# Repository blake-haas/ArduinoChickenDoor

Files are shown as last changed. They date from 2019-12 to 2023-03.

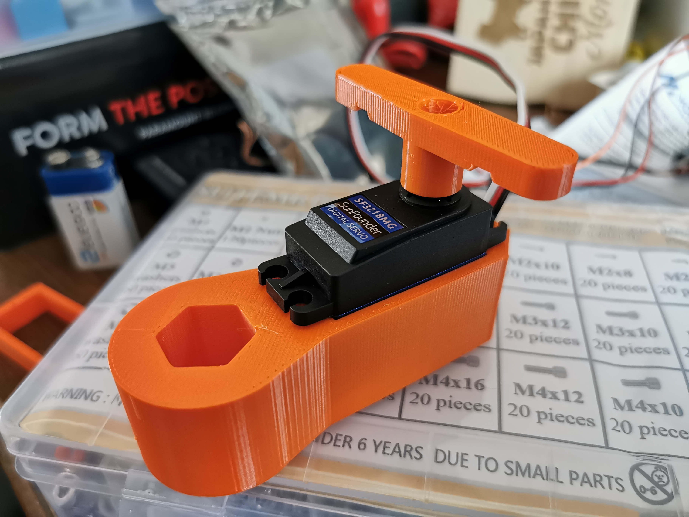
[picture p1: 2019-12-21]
IMG_20191218_131732.jpg

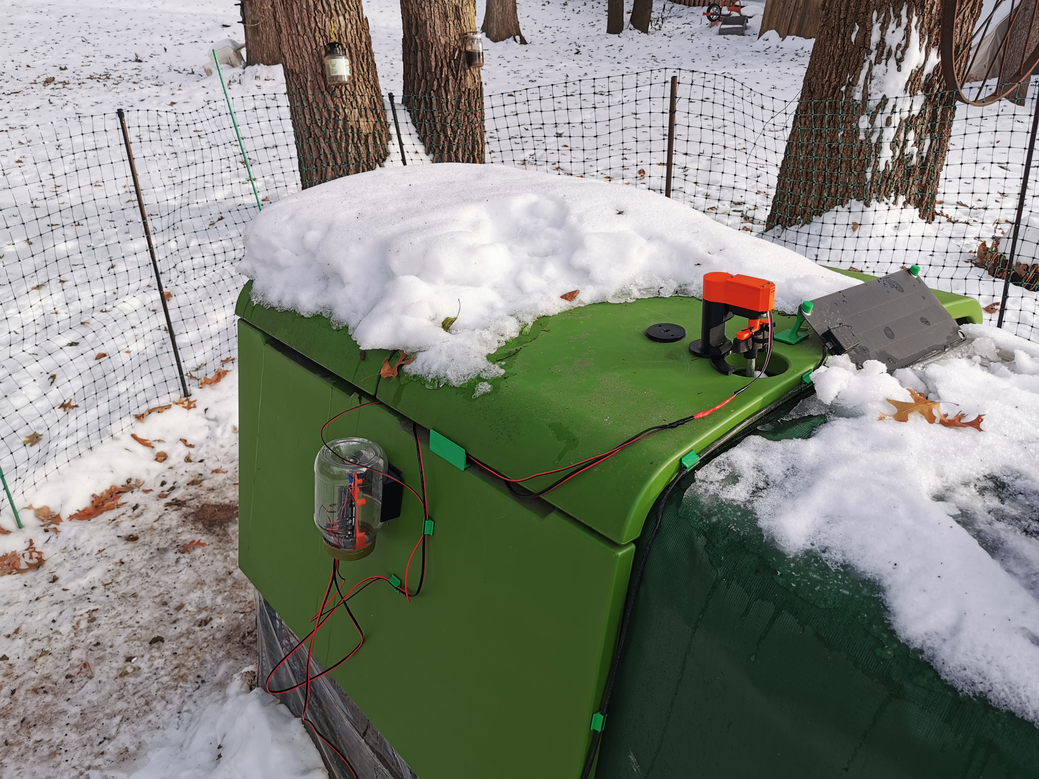
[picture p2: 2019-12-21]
IMG_20191221_142228.jpg

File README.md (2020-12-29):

# ArduinoChickenDoor
Automatic door for chicken coop (eglu cube) | Can be adapted to work with any coop.
Designed for very low power usage.

This is a project for an automatic chicken door based on light levels.
Door closes at around 19 lux and opens after 50 lux.

Parts list:
1. Arduino Uno / Mini / micro
2. SunFounder 20KG Servo Motor Waterproof High Torque Servo, SF3218MG Metal Gear Digital Servo
3. LM393 Digital Light Intensity Photosensitive Sensor Module for Arduino UNO
4. Power source 9v / 12v. For me it was a 12v tractor battery with a LM2596s Buck Converter tuned to 9v. 
5. Wires and a clear container to mount the light sensing hardware (mayo jar for me).
6. A 3d printer to print my designed parts for the eglu cube or your own diy solution for your coop.
7. Misc M2, M3 and M4 bolts for my designed parts.
8. Silicone / Gasket maker to seal the servo body if using my designed parts (Not Necessary if using ServoCoverBody_ClosedTop).

This has lasted through a winter and is doing great!
Enancements after summer and winter use:
I RECOMMEND USING THE ServoStand_v2_Short.stl WITH THE ServoHandleAdapter.stl. It has better alignment and smoother operation!
CHECK OUT THE WIRE DIAGRAM (AutoChickenDoorCoopWireDiagram.png) for the simplest installation.

Get a metal T spline Metal Aluminum 25T Servo Horn, the printed one will eventually fail.

Wire in a 5vdc converter to have a solid 5v off of the main 9v power vs having the arduino try to handle the load (my uno handles it but just barely).

I also wired up some 3 Pin Way Car Waterproof Wire Connector Plug Auto Electrical Wire Connectors so that i can easily disconnect the system if i needed
to troubleshoot anything.

I added some DIY Battery Pack PVC Heat Shrink Wrap Tube 180±3MM to the jar on the bottom third to act like a skirt to allow water to flow AWAY
from the jar lid. This keeps the entire inside of the jar bone dry while still allowing me to unscrew the lid for access.

Im located in minnesota. I upgraded my power source (battery) to a full 12v car battery to power this thing and i use a 30w solar panel to trickle charge it all day.
It works flawlessly this way all summer. In the winter i have a trickle charger plugged in via extension cord to keep it topped off.

Lastly, I covered the uno and electronics in some clear nail polish to protect from moisture (just in case).

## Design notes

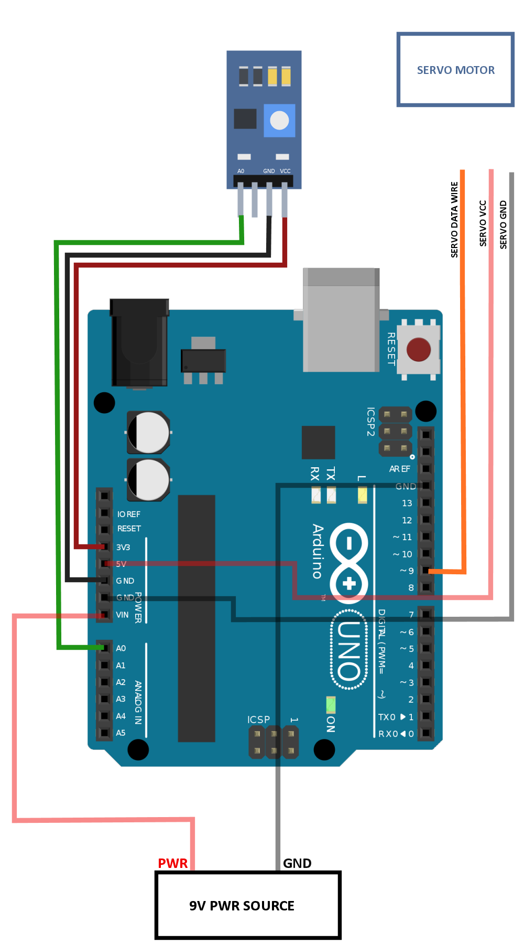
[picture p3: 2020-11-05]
AutoChickenDoorCoopWireDiagram.png

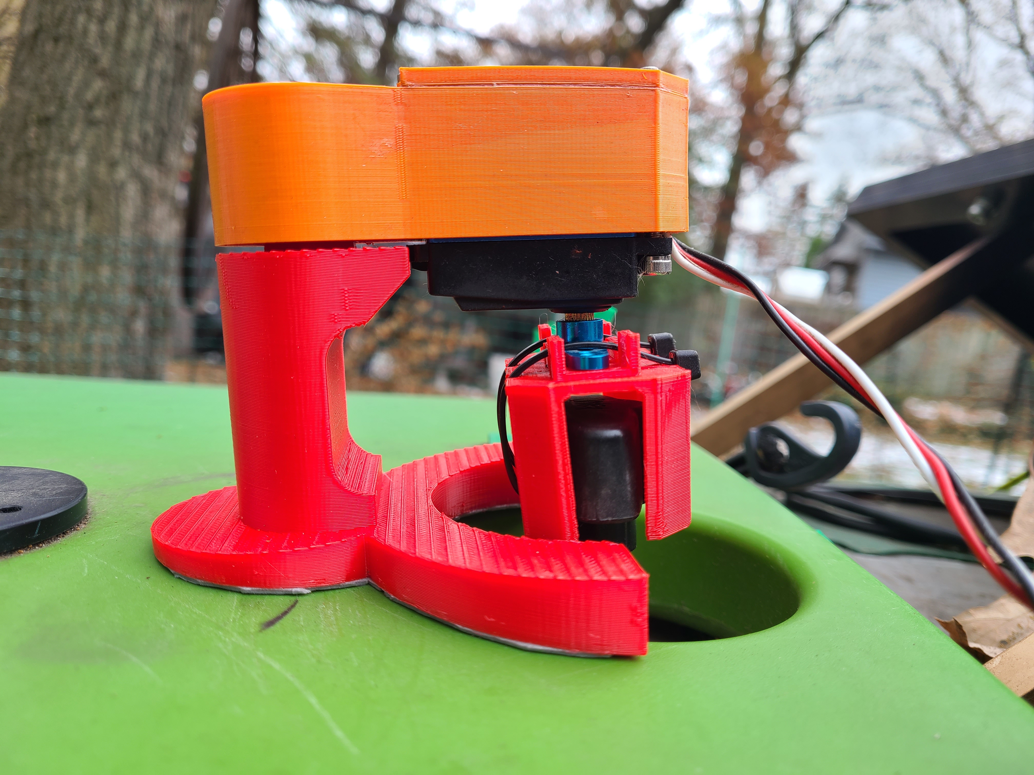
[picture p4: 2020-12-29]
2020-10-29 10.03.07.jpg

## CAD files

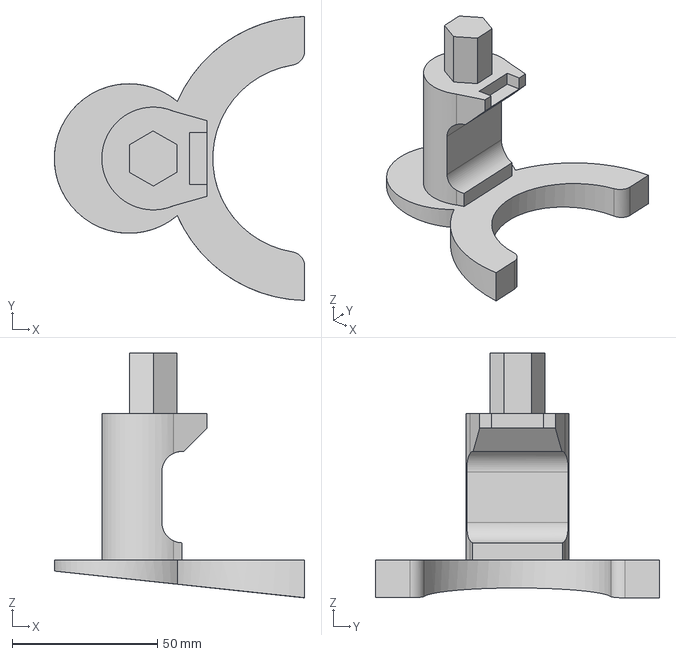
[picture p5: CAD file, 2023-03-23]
ChickenCoopServoBaseV2.step
86.1 x 97.6 x 84.2 mm

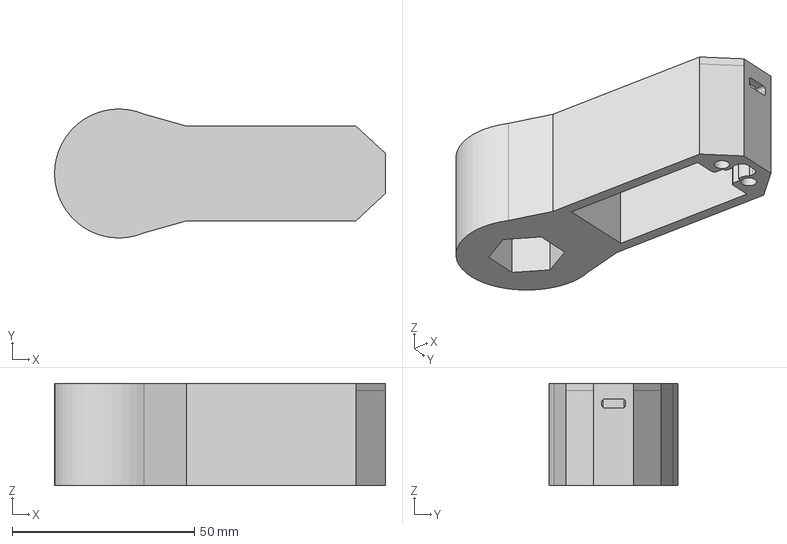
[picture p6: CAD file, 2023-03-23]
ChickenCoopServoCoverBodyModel.step
90.8 x 35.3 x 28.0 mm

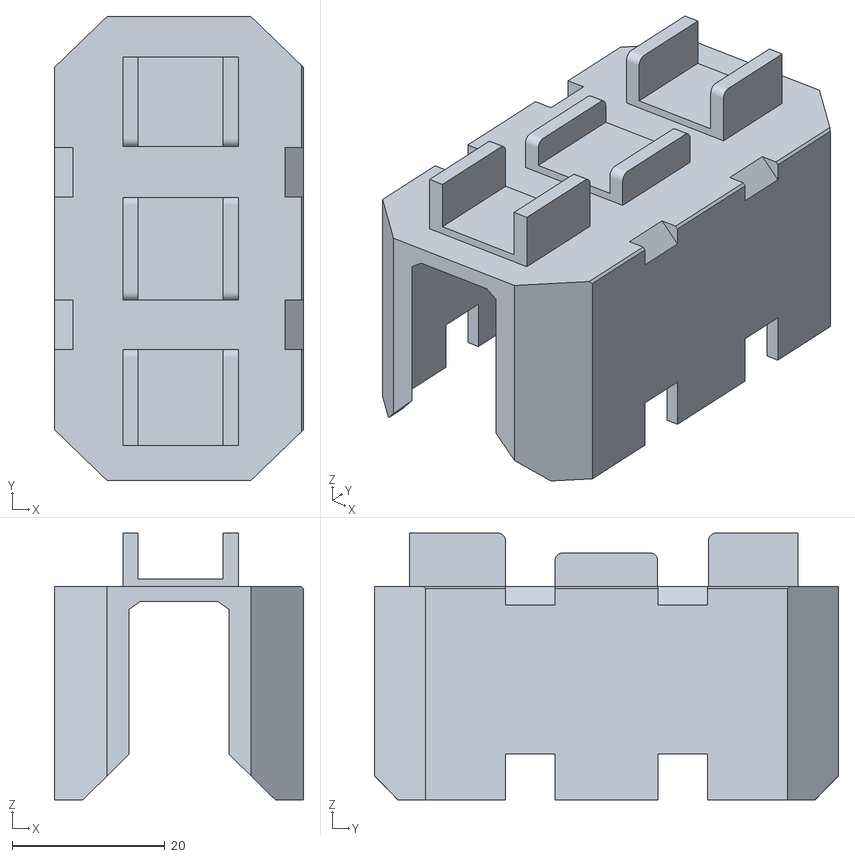
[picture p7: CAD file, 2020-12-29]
ServoHandleAdapter.stl
32.7 x 60.8 x 35.0

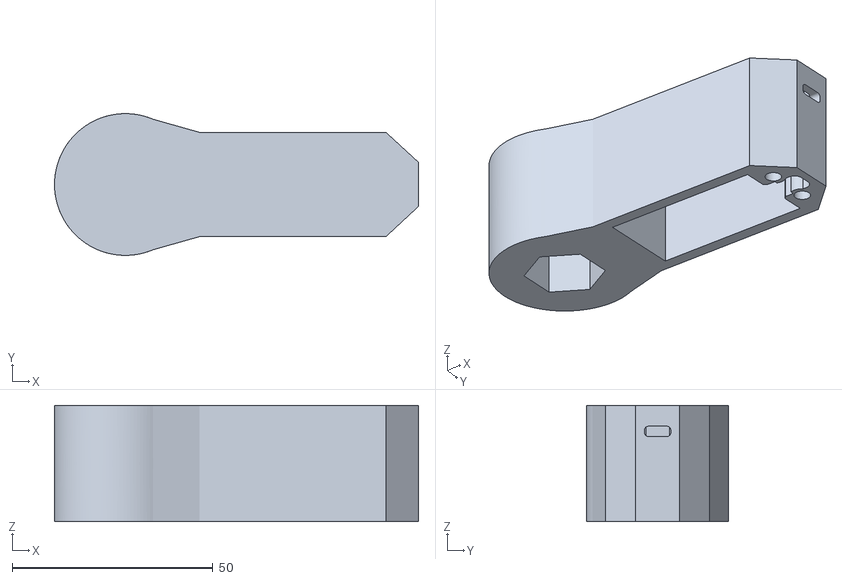
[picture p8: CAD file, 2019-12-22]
ServoCoverBody_ClosedTop.stl
90.8 x 35.3 x 29.0

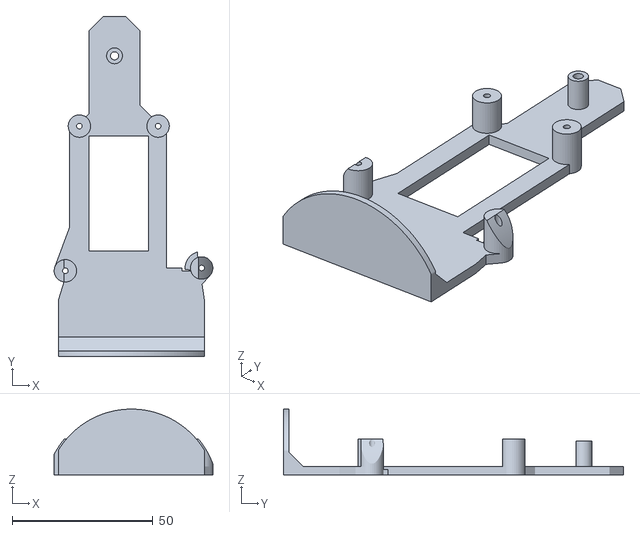
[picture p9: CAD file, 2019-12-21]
ArduinoUnoMountMayoJarLid.stl
56.5 x 121.0 x 23.4

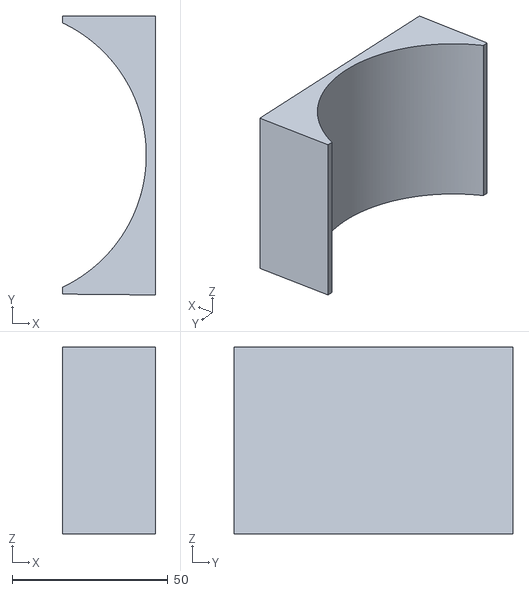
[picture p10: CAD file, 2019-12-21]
JarAttachment.stl
30.0 x 89.7 x 60.0

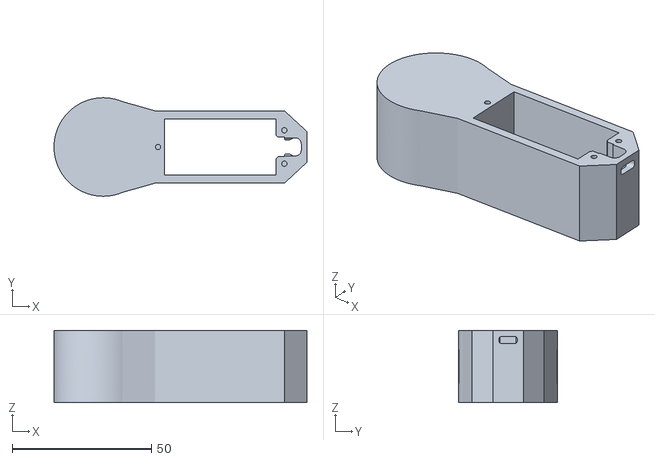
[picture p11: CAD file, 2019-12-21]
ServoCoverBody.stl
90.8 x 35.4 x 26.0

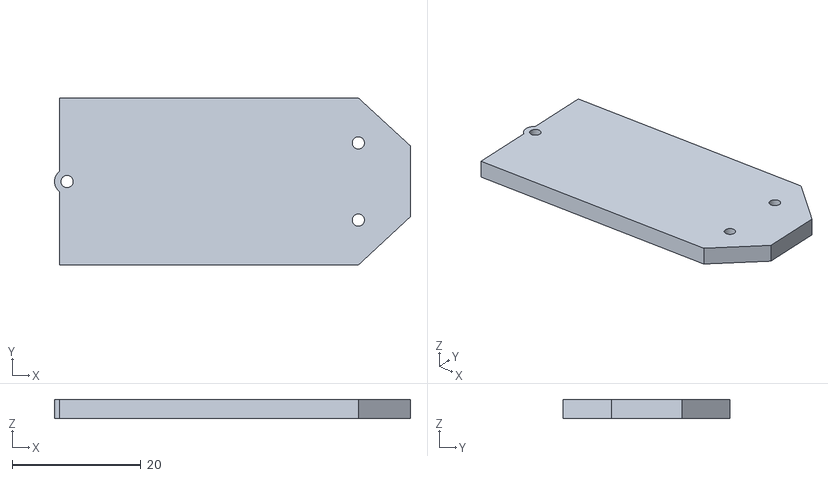
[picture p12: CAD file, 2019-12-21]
ServoCoverTop.stl
55.4 x 26.0 x 3.00

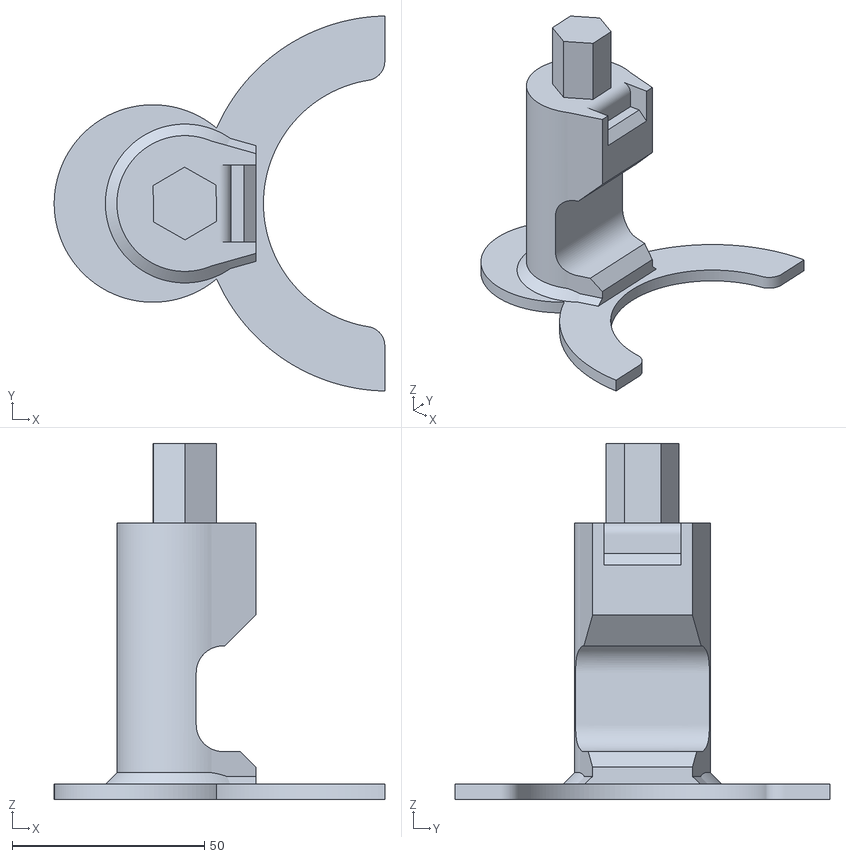
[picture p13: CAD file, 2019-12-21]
ServoStand.stl
86.1 x 97.6 x 92.7

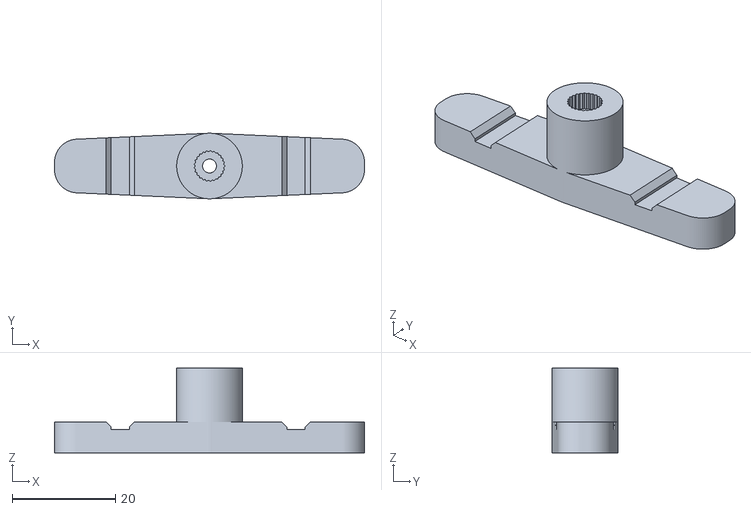
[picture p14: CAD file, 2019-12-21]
ServoHub.stl
60.0 x 12.7 x 16.4

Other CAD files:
ServoStand_v2_Short.stl

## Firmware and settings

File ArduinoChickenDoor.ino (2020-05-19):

#include <Servo.h>
#include <avr/wdt.h>            // library for default watchdog functions
#include <avr/interrupt.h>      // library for interrupts handling
#include <avr/sleep.h>          // library for sleep
#include <avr/power.h>          // library for power control

int SERVO_PIN = 9;
int LIGHT_SENSOR_ANALOG_PIN = A0;
int LOW_LIGHT_THRESHOLD = 500; // ~1.3 lux You need to calibrate this against a lux meter, each sensor has its own resistance values.
int HIGH_LIGHT_THRESHOLD = 210; // ~24 lux
int HIGH_LIGHT_HIT_COUNT = 15; // 15 min
int LOW_LIGHT_HIT_COUNT = 20; // 20 min
int LowLightCount = 0;
int HighLightCount = 0;
int DoorState = 0; // 0 is unknown // 1 is open // 2 is closed
int pos = 25;
Servo Servo1;
int nbr_remaining; // how many times remain to sleep before wake up 

// interrupt raised by the watchdog firing
// when the watchdog fires during sleep, this function will be executed
// remember that interrupts are disabled in ISR functions
ISR(WDT_vect)
{
        // not hanging, just waiting
        // reset the watchdog
        wdt_reset();
}
// function to configure the watchdog: let it sleep 8 seconds before firing
// when firing, configure it for resuming program execution
void configure_wdt(void)
{
 
  cli();                           // disable interrupts for changing the registers

  MCUSR = 0;                       // reset status register flags

                                   // Put timer in interrupt-only mode:                                       
  WDTCSR |= 0b00011000;            // Set WDCE (5th from left) and WDE (4th from left) to enter config mode,
                                   // using bitwise OR assignment (leaves other bits unchanged).
  WDTCSR =  0b01000000 | 0b100001; // set WDIE: interrupt enabled
                                   // clr WDE: reset disabled
                                   // and set delay interval (right side of bar) to 8 seconds

  sei();                           // re-enable interrupts

  // reminder of the definitions for the time before firing
  // delay interval patterns:
  //  16 ms:     0b000000
  //  500 ms:    0b000101
  //  1 second:  0b000110
  //  2 seconds: 0b000111
  //  4 seconds: 0b100000
  //  8 seconds: 0b100001
 
}
// Put the Arduino to deep sleep. Only an interrupt can wake it up.
void sleep(int ncycles)
{  
  nbr_remaining = ncycles; // defines how many cycles should sleep

  // Set sleep to full power down.  Only external interrupts or
  // the watchdog timer can wake the CPU!
  set_sleep_mode(SLEEP_MODE_PWR_DOWN);
 
  // Turn off the ADC while asleep.
  power_adc_disable();
 
  while (nbr_remaining > 0){ // while some cycles left, sleep!

  // Enable sleep and enter sleep mode.
  sleep_mode();

  // CPU is now asleep and program execution completely halts!
  // Once awake, execution will resume at this point if the
  // watchdog is configured for resume rather than restart
 
  // When awake, disable sleep mode
  sleep_disable();
  
  // we have slept one time more
  nbr_remaining = nbr_remaining - 1;
 
  }
 
  // put everything on again
  power_all_enable();
 
}
void setup() {
  // put your setup code here, to run once:
  //Serial.begin(115200);
  //while (! Serial) {}  // wait for serial monitor to attach
  // Initialize the door open.
  openDoor();
  delay(20);
  // configure the watchdog
  configure_wdt();
}

void loop() {
  int16_t currentLightLevel = analogRead(LIGHT_SENSOR_ANALOG_PIN);
  setLightLevel(currentLightLevel);
  if (HighLightCount == HIGH_LIGHT_HIT_COUNT && DoorState != 1) {
//    Serial.print("HighLightCount: ");
//    Serial.print(HighLightCount);
//    Serial.println("");
//    Serial.print("LowLightCount: ");
//    Serial.print(LowLightCount);
//    Serial.println("");
//    Serial.println("opening door!");
//    Serial.print("Previous DoorState: ");
//    Serial.print(DoorState);
//    Serial.println("");
    // Open the Door
    openDoor();
  }
  if (LowLightCount == LOW_LIGHT_HIT_COUNT && DoorState != 2) {
//    Serial.print("HighLightCount: ");
//    Serial.print(HighLightCount);
//    Serial.println("");
//    Serial.print("LowLightCount: ");
//    Serial.print(LowLightCount);
//    Serial.println("");
//    Serial.println("closing door!");
//    Serial.print("Previous DoorState: ");
//    Serial.print(DoorState);
//    Serial.println("");
    // Close the Door
    closeDoor();
  }
  sleep(8); // sleep for 1 min..
}
void setLightLevel(int16_t level) {
  if (level >= LOW_LIGHT_THRESHOLD) {
    // We got a low light value, RESET the high count
    HighLightCount = 0;
    LowLightCount = LowLightCount + 1;
    if (LowLightCount < LOW_LIGHT_HIT_COUNT) {
      // stop incrementing
      LowLightCount = LowLightCount + 1;
    }
  } else if (level <= HIGH_LIGHT_THRESHOLD) {
    // We got a high light value, RESET the low count
    LowLightCount = 0;
    if (HighLightCount < HIGH_LIGHT_HIT_COUNT) {
      // stop incrementing
      HighLightCount = HighLightCount + 1;
    }
  }
//  Serial.print("Lux: ");
//  Serial.print(level);
//  Serial.println("");
}
void openDoor() {
  Servo1.attach(SERVO_PIN, 500, 2500);
  for (pos = 160; pos >= 25; pos -= 1) {
    // goes from 160 degrees to 25 degrees
    // in steps of 1 degree
    Servo1.write(pos);
    delay(50);
  }
  DoorState = 1;
  Servo1.detach();
  delay(7000); // Wait for servo to finish movements
}

void closeDoor() {
  Servo1.attach(SERVO_PIN, 500, 2500);
  for (pos = 25; pos <= 160; pos += 1) {
    // goes from 25 degrees to 160 degrees
    Servo1.write(pos);
    delay(50);
  }
  DoorState = 2;
  Servo1.detach();
  delay(7000); // Wait for servo to finish movements
}

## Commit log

2019-12-21 Add files via upload
    Initial checkin of arduino uno automatic chicken door.
2019-12-21 Added STL's and images of final version 1 installation
    [JarAttachment.stl, ServoCoverBody.stl, ServoCoverTop.stl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]
2019-12-22 Added STL for servo body with top closed
    [ServoCoverBody_ClosedTop.stl]
2020-05-19 Update ArduinoChickenDoor.ino
    Implemented different hit counts for open and close logic. It now takes 20 minutes to close vs 15 to open.
2020-10-30 Added updated servo stand and added a coupler
    [EgluDoorOpenerAdapter_refined_centered.stl, ServoStand_v2_Short.stl]
2020-11-05 added wire diagram
2020-12-29 Updating files, removed old picture, added new picture, edited readme
    [EgluDoorOpenerAdapter_refined_centered.stl, ServoHandleAdapter.stl]
2023-03-23 Adding Step files for better alteration
    [ChickenCoopServoBaseV2.step, ChickenCoopServoCoverBodyModel.step]
